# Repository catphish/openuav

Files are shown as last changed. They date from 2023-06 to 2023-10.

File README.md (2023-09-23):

# OpenUAV
OpenUAV is an open source flight controller for multirotors with
a focus on FPV. It is currently in active development.

# Features
* ACRO and ANGLE flight modes
* DSHOT
* ELRS
* Blackbox flight recorder
* USB configuration tool
* Canvas OSD

# Roadmap
* Tidy up and comment all current code
* USB configuration tool
* More OSD options

# Dependencies

## ArchLinux-based distributions

```sh
sudo pacman -Sy arm-none-eabi-binutils arm-none-eabi-gcc arm-none-eabi-newlib \
                dfu-util \
                stlink
```

# Configurator

The USB configurator can be used to configure the quad, and also to download blackbox
logs.

## Configuration

You can view the current configuration by running `configurator get`.

The commands to set configuration are a little cryptic. Use command `configurator set x y z`, where `x` is the
categry number, `y` is the specific entry number, and `z` is the value to set. Please refer to the following file
for the category and entry numbers: https://github.com/catphish/openuav/blob/master/configurator/usb.h

## Motor configuration

The motor configuration is also not very intuitive, but works as follows. First select "props in" `configurator set 3 5 0`
or "props out" `configurator set 3 5 1`.

Next, map the motor outputs using the command: `configurator set 3 x y`, where `x` is the motor output pin (1-4), and `y` is
a corner of the quad according to the following table:

```
0: no output
1: rear left
2: front right
3: front left
4: rear right
```

* NOTE: Due to the way air mode currently works, motors set to zero outout will still spin at minimum RPM. This needs fixing.

## Black Box

Data will be recorded to the black box any time the quad is armed and will continue until the memory
is full (approx 10 minutes flight time). You can erase the black box with `configurator erase`.

You can download the blackbox data with `configurator read > data.csv`. The CSV can be processed
with any tool of your choosing but I find kst2 to be the best.

# Basic Tuning Guide

Tuning should be done in acro mode at a rate you are comfortable with. I use a rate
of 1200 (840 dps) for this process.

## Part 1 - P term

Set the I and D terms to zero so that they don't interfere. Start with a low value (P=50).
Increase P until the quad is sufficiently responsive to stick inputs. You can expect a
little bounceback.
In the 5 inch development quad, the P value is 120.

## Part 2 - D term

Increase the D term only as much as is required to prevent the bounceback.
In the 5 inch development quad, the D value is 150.

## Part 3 - I term

Increase the I term only as much as is required to prevent drift. You may find that this
needs to be increased more when flying in strong wind. Higher values will make the quad
more stable but will introduce some bouncenback when performing flips.
In the 5 inch development quad, the I value is 50.

## Part 4 - Z rates

There is currently no specific process for tuning the Z rates. Values of 200 and 200
for P and I seem to work in most cases. If there is yaw drift then it may be necessary
to increase one or the other. Increase the I term in the case of slow drift or the P
term in the case of sudden yaw disruption.

# Tuning Examples

## TBS Source One V5 5" - 2306/2555KV Motors at 4S

```
Angle rate: 1000
Acro rate: 1000
P: 100
I: 80
D: 100
Yaw P: 200
Yaw I: 100
Expo: 60
Yaw expo: 60
Throttle gain: 80
Throttle min: 200
```

## iFlight iX3 Racer V1 3" - 1104/5250KV Motors at 3S

THIS TUNE IS STILL UNDERGOING TESTING

```
Angle rate (sR): 670
Acro rate (sr): 670
P (sp): x
I (si): x
D (sd): x
Yaw P (sy): 220
Yaw I (sY): 200
Expo (se): 25
Yaw expo (sE): 30
Throttle gain (st): 80
Throttle min (sT): 100
```

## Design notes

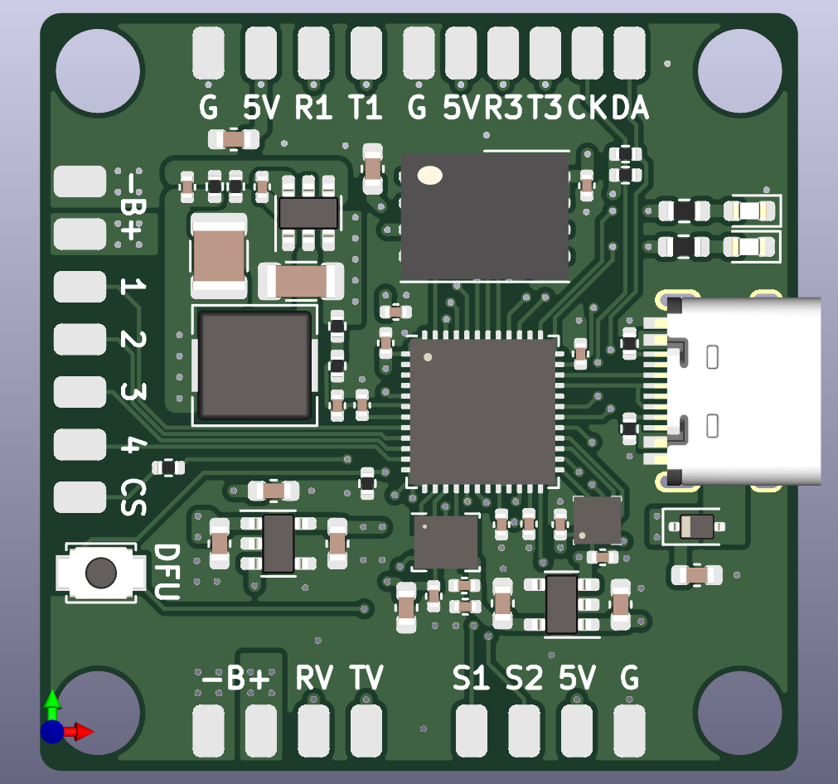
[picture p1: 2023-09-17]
hardware/openuav.png

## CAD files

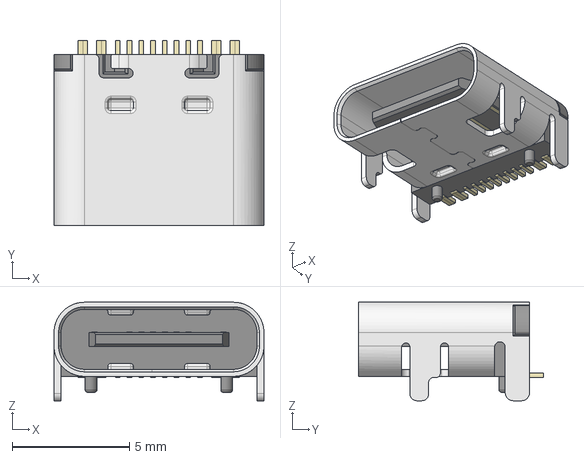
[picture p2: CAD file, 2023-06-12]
hardware/3d/HRO_TYPE-C-31-M-12.step
8.95 x 7.90 x 4.20 mm

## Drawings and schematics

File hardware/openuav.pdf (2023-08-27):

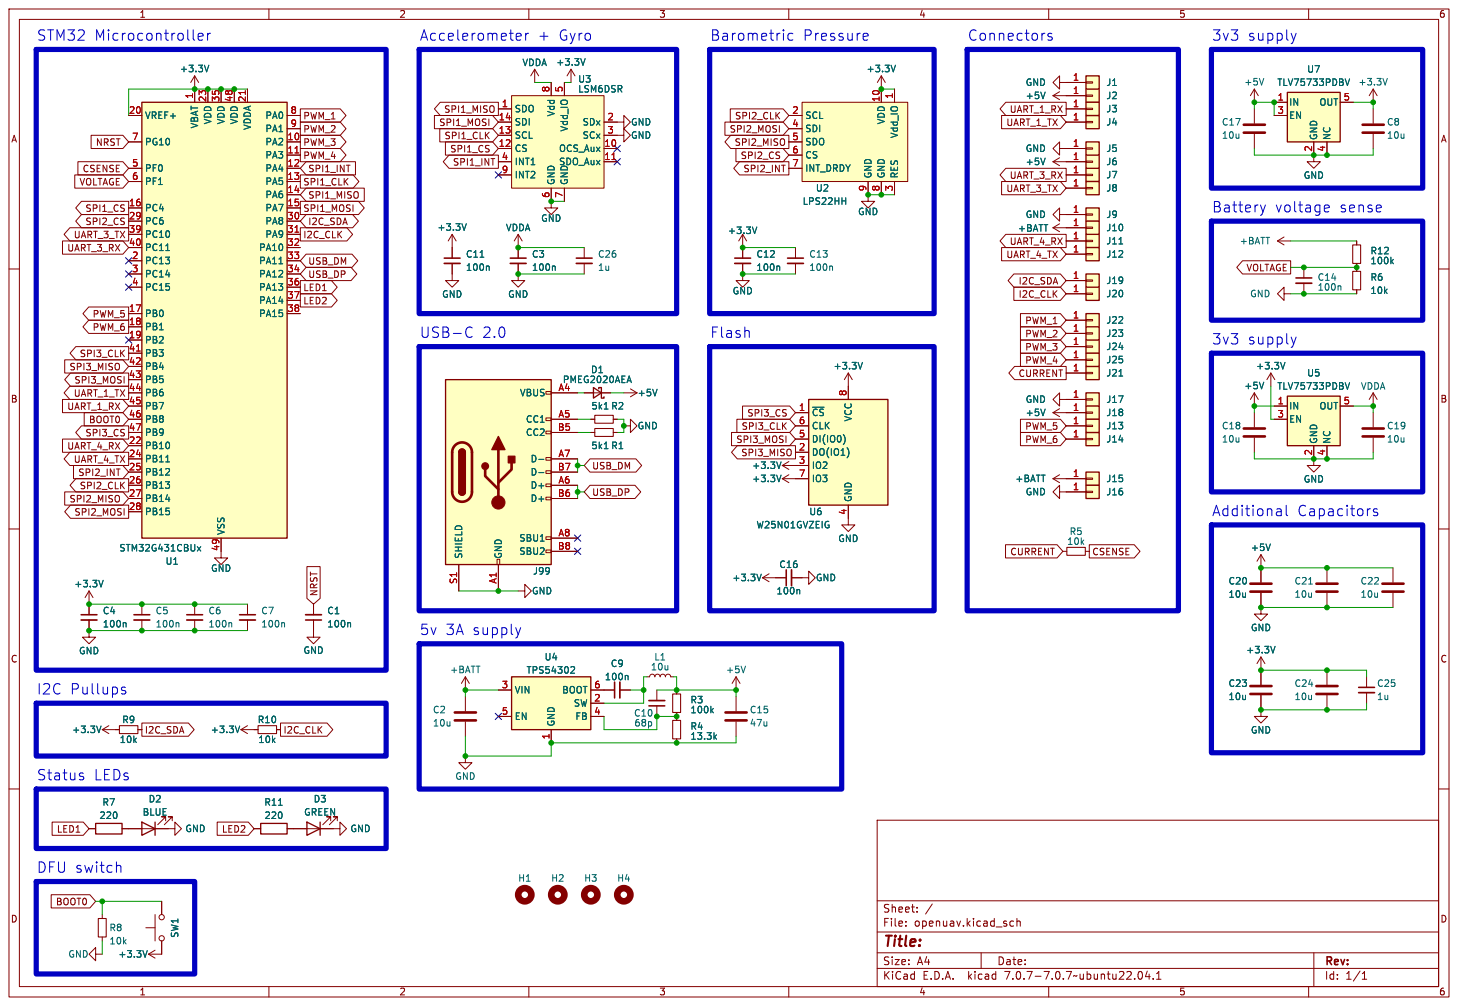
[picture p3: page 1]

1 PA2 10 PA3 11 PA4 12 PA5 13 PA6 14 PA7 15 PC4 16 PB0 17 PB1 18 PB2 19 PC13 2 VREF+ 20 VDDA 21 PB10 22 VDD 23 PB11 24 PB12 25 PB13 26 PB14 27 PB15 28 PC6 29 PC14 3 PA8 30 PA9 31 PA10 32 PA11 33 PA12 34 VDD 35 PA13 36 PA14 37 PA15 38 PC10 39 PC15 4 PC11 40 PB3 41 PB4 42 PB5 43 PB6 44 PB7 45 PB8 46 PB9 47 VDD 48 VSS 49 PF0 5 PF1 6 PG10 7 PA0 8 PA1 9 +3.3V SW1 +3.3V R9

1 PA2 10 PA3 11 PA4 12 PA5 13 PA6 14 PA7 15 PC4 16 PB0 17 PB1 18 PB2 19 PC13 2 VREF+ 20 VDDA 21 PB10 22 VDD 23 PB11 24 PB12 25 PB13 26 PB14 27 PB15 28 PC6 29 PC14 3 PA8 30 PA9 31 PA10 32 PA11 33 PA12 34 VDD 35 PA13 36 PA14 37 PA15 38 PC10 39 PC15 4 PC11 40 PB3 41 PB4 42 PB5 43 PB6 44 PB7 45 PB8 46 PB9 47 VDD 48 VSS 49 PF0 5 PF1 6 PG10 7 PA0 8 PA1 9 U1 STM32G431CBUx R3

1 SW 2 VIN 3 FB 4 EN 5 BOOT 6 U4 +BATT TPS54302

1 SW 2 VIN 3 FB 4 EN 5 BOOT 6 +3.3V R10

Id: 1/1 Title: File: openuav.kicad_sch Sheet: /

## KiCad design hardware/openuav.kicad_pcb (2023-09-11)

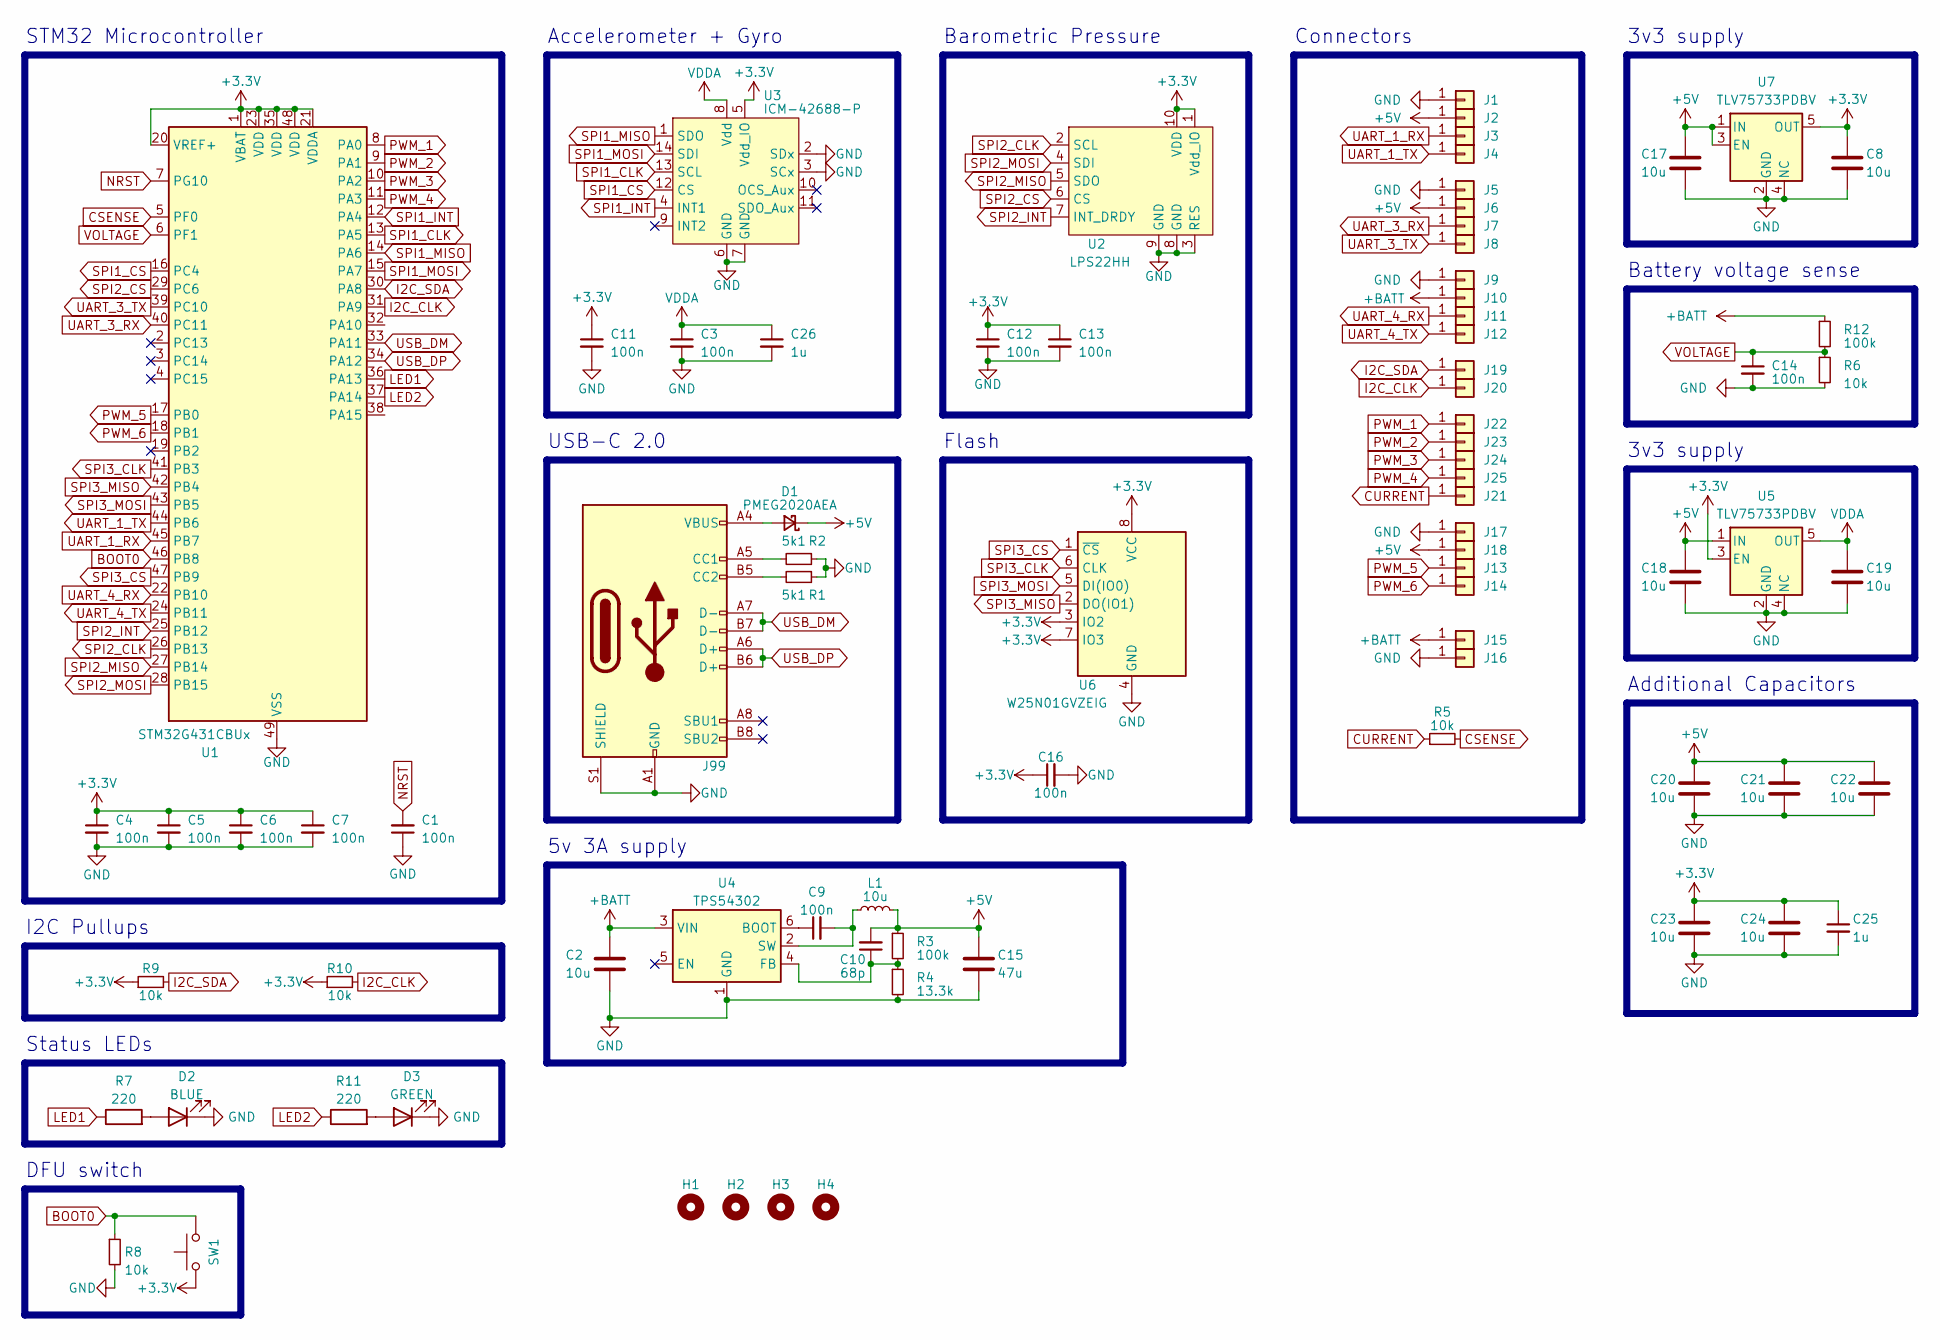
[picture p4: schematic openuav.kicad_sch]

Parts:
C1, C3, C4, C5, C6, C7, C9, C11, C12, C13, C14, C16: 100n; C_0402_1005Metric; LCSC C1525
C2: 10u; C_1206_3216Metric; LCSC C13585
C8, C17, C18, C19, C20, C21, C22, C23, C24: 10u; C_0603_1608Metric; LCSC C19702
C10: 68p; C_0402_1005Metric; LCSC C14441
C15: 47u; C_1210_3225Metric; LCSC C77101
C25, C26: 1u; C_0402_1005Metric; LCSC C52923
D1: PMEG2020AEA; D_SOD-323; LCSC C389354
D2: BLUE; LED_0603_1608Metric; LCSC C72041
D3: GREEN; LED_0603_1608Metric; LCSC C72043
H1, H2, H3, H4: MountingHole; MountingHole_4mm
J1, J2, J3, J4, J5, J6, J7, J8, J9, J10, J11, J12, J13, J14, J15, J16, J17, J18, J19, J20, J21, J22, J23, J24, J25: Conn_01x01; smallpad
J99: USB_C_Receptacle_USB2.0; TYPE-C-31-M-12; LCSC C165948
L1: 10u; L_Sunlord_MWSA0503S; LCSC C408412
R1, R2: 5k1; R_0402_1005Metric; LCSC C25905
R3, R12: 100k; R_0402_1005Metric; LCSC C25741
R4: 13.3k; R_0402_1005Metric; LCSC C274352
R5, R6, R8, R9, R10: 10k; R_0402_1005Metric; LCSC C25744
R7, R11: 220; R_0603_1608Metric; LCSC C22962
SW1: SW_Push; SW_SPST_B3U-1000P; LCSC C231329
U1: STM32G431CBUx; QFN-48-1EP_7x7mm_P0.5mm_EP5.6x5.6mm; LCSC C529356
U2: LPS22HH; ST_HLGA-10_2x2mm_P0.5mm_LayoutBorder3x2y; LCSC C2827824
U3: ICM-42688-P; LGA-14_3x2.5mm_P0.5mm_LayoutBorder3x4y; LCSC C1850418
U4: TPS54302; SOT-23-6; LCSC C311983
U5, U7: TLV75733PDBV; SOT-23-5; LCSC C485517
U6: W25N01GVZEIG; WSON-8-1EP_8x6mm_P1.27mm_EP3.4x4.3mm; LCSC C907680

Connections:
+3V3: C4.1, C5.1, C6.1, C7.1, C8.1, C11.1, C12.1, C13.1, C16.1, C23.1, C24.1, C25.1, R9.1, R10.1, SW1.1, U1.1 (VBAT), U1.20 (VREF+), U1.21 (VDDA), U1.23 (VDD), U1.35 (VDD), U1.48 (VDD), U2.1 (Vdd_IO), U2.10 (VDD), U3.5 (Vdd_IO), U5.3 (EN), U6.3 (IO2), U6.7 (IO3), U6.8 (VCC), U7.5 (OUT)
+5V: C10.2, C15.1, C17.1, C18.1, C20.1, C21.1, C22.1, D1.1 (K), J2.1, J6.1, J18.1, L1.2, R3.1, U5.1 (IN), U7.1 (IN), U7.3 (EN)
+BATT: C2.1, J10.1, J15.1, R12.1, U4.3 (VIN)
BOOT0: R8.1, SW1.2, U1.46 (PB8)
CSENSE: R5.2, U1.5 (PF0)
CURRENT: J21.1, R5.1
GND: C1.1, C2.2, C3.2, C4.2, C5.2, C6.2, C7.2, C8.2, C11.2, C12.2, C13.2, C14.2, C15.2, C16.2, C17.2, C18.2, C19.2, C20.2, C21.2, C22.2, C23.2, C24.2, C25.2, C26.2, D2.1 (K), D3.1 (K), J1.1, J5.1, J9.1, J16.1, J17.1, J99.A1 (GND), J99.A12 (GND), J99.B1 (GND), J99.B12 (GND), J99.S1 (SHIELD), R1.1, R2.1, R4.2, R6.2, R8.2, U1.49 (VSS), U2.3 (RES), U2.8 (GND), U2.9 (GND), U3.2 (SDx), U3.3 (SCx), U3.6 (GND), U3.7 (GND), U4.1 (GND), U5.2 (GND), U5.4 (NC), U6.4 (GND), U7.2 (GND), U7.4 (NC)
I2C_CLK: J20.1, R10.2, U1.31 (PA9)
I2C_SDA: J19.1, R9.2, U1.30 (PA8)
LED1: R7.1, U1.36 (PA13)
LED2: R11.1, U1.37 (PA14)
NRST: C1.2, U1.7 (PG10)
unnamed: D1.2 (A), J99.A4 (VBUS), J99.A9 (VBUS), J99.B4 (VBUS), J99.B9 (VBUS)
unnamed: D2.2 (A), R7.2
unnamed: D3.2 (A), R11.2
unnamed: J99.A5 (CC1), R2.2
unnamed: J99.B5 (CC2), R1.2
unnamed: C9.1, U4.6 (BOOT)
unnamed: C10.1, R3.2, R4.1, U4.4 (FB)
unnamed: C9.2, L1.1, U4.2 (SW)
PWM_1: J22.1, U1.8 (PA0)
PWM_2: J23.1, U1.9 (PA1)
PWM_3: J24.1, U1.10 (PA2)
PWM_4: J25.1, U1.11 (PA3)
PWM_5: J13.1, U1.17 (PB0)
PWM_6: J14.1, U1.18 (PB1)
SPI1_CLK: U1.13 (PA5), U3.13 (SCL)
SPI1_CS: U1.16 (PC4), U3.12 (CS)
SPI1_INT: U1.12 (PA4), U3.4 (INT1)
SPI1_MISO: U1.14 (PA6), U3.1 (SDO)
SPI1_MOSI: U1.15 (PA7), U3.14 (SDI)
SPI2_CLK: U1.26 (PB13), U2.2 (SCL)
SPI2_CS: U1.29 (PC6), U2.6 (CS)
SPI2_INT: U1.25 (PB12), U2.7 (INT_DRDY)
SPI2_MISO: U1.27 (PB14), U2.5 (SDO)
SPI2_MOSI: U1.28 (PB15), U2.4 (SDI)
SPI3_CLK: U1.41 (PB3), U6.6 (CLK)
SPI3_CS: U1.47 (PB9), U6.1 (~CS)
SPI3_MISO: U1.42 (PB4), U6.2 (DO(IO1))
SPI3_MOSI: U1.43 (PB5), U6.5 (DI(IO0))
UART_1_RX: J3.1, U1.45 (PB7)
UART_1_TX: J4.1, U1.44 (PB6)
UART_3_RX: J7.1, U1.40 (PC11)
UART_3_TX: J8.1, U1.39 (PC10)
UART_4_RX: J11.1, U1.22 (PB10)
UART_4_TX: J12.1, U1.24 (PB11)
USB_DM: J99.A7 (D-), J99.B7 (D-), U1.33 (PA11)
USB_DP: J99.A6 (D+), J99.B6 (D+), U1.34 (PA12)
VDDA: C3.1, C19.1, C26.1, U3.8 (Vdd), U5.5 (OUT)
VOLTAGE: C14.1, R6.1, R12.2, U1.6 (PF1)

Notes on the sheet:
Accelerometer + Gyro
DFU switch
Status LEDs
3v3 supply
Additional Capacitors
5v 3A supply
Flash
Barometric Pressure
STM32 Microcontroller
Connectors
I2C Pullups
USB-C 2.0
Battery voltage sense

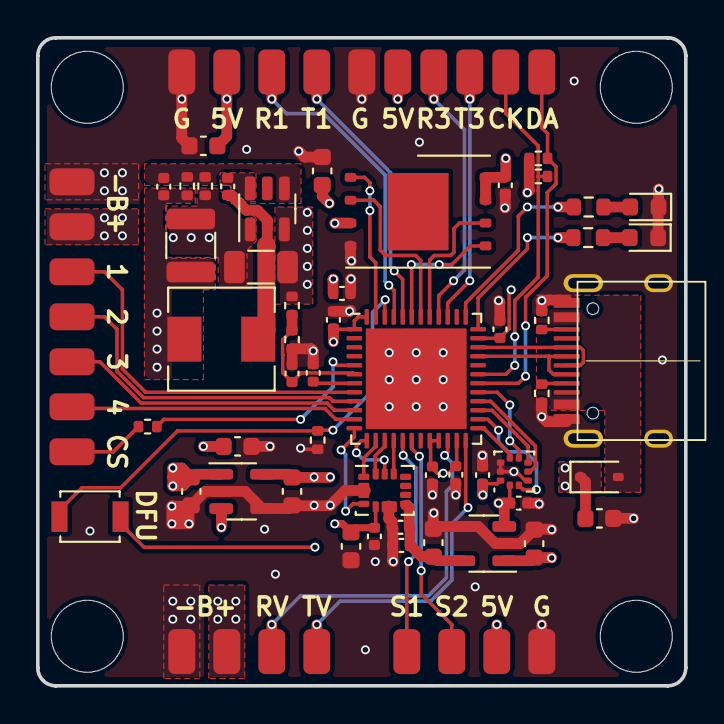
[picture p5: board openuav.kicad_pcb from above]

Board: 4 copper layers, 36.0 x 36.0 mm, 80 parts (0 on the bottom side), 50 nets.

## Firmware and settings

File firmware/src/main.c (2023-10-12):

#include <stm32g4xx.h>
#include <string.h>
#include <stdio.h>
#include <stdint.h>
#include "gpio.h"
#include "usb.h"
#include "dshot.h"
#include "led.h"
#include "util.h"
#include "spi.h"
#include "elrs.h"
#include "uart.h"
#include "clock.h"
#include "gyro.h"
#include "imu.h"
#include "quaternion.h"
#include "adc.h"
#include "msp.h"
#include "settings.h"
#include "flash.h"
#include "blackbox.h"
#include "airmode.h"
#include "main.h"
#include "barometer.h"

// Set up all the hardware. Each part of the hardware has its own
// module of code with its own init function.
void SystemInit(void) {
  clock_init();
  msleep(200);
  gpio_init();
  led_init();
  usb_init();
  dshot_init();
  spi_init();
  uart_init();
  gyro_init();
  imu_zero();
  baro_init();
  adc_init();
  flash_init();
  blackbox_init();
}

// This struct contains the data that will be output to the four motors.
static struct dshot_data dshot;

// Create a ring buffer of the last GYRO_BUFFER_SIZE gyro readings.
// This will be used to calculate the D term.
#define GYRO_BUFFER_SIZE 60
static struct gyro_data gyro_buffer[GYRO_BUFFER_SIZE];
static uint8_t gyro_buffer_index = 0;

int main(void) {
  // This flag inhibits arming at power-on, and is set to 1 when it's safe to arm.
  uint8_t arming_allowed = 0;

  // These variables are used to store the accumulated integral term for each axis.
  float i_pitch = 0;
  float i_roll  = 0;
  float i_yaw   = 0;

  // A counter to keep track of the number of frames since arming. Used only by the gyro calibration routine.
  uint32_t arm_counter = 0;

  // A continuously increasing counter that is used to timestamp blackbox frames.
  uint32_t frame_count = 0;

  // LED2 is the power LED, turn it on before we do anything else.
  led2_on();

  // Load settings from flash.
  settings_read();

  // Main loop. This runs as fast as possible, but the majority of the code is located
  // within an if block that only runs each time data is received from the gyro.
  while(1) {
    // Poll the USB peripheral to transmit and receive data as needed.
    usb_main();
    // Poll the UART peripheral to transmit pending data. Receiving of data is handled by interrupts.
    uart_tx();
    // Process MSP requests and transmit responses. This also transmits OSD data.
    msp_send_response();

    // Each time the gyro has new data, we run the main control loop.
    if(gyro_ready()) {
      // Fetch settings and scale them to the appropriate units.
      volatile struct settings *settings = settings_get();
      float angle_rate    = 10.f      * settings->angle_rate;
      float acro_rate     = 0.01f     * settings->acro_rate;
      float p             = 0.001f    * settings->p;
      float i             = 0.000001f * settings->i;
      float d             = 0.001f    * settings->d;
      float yaw_p         = 0.001f    * settings->yaw_p;
      float yaw_i         = 0.000001f * settings->yaw_i;
      float expo          = 0.01f     * settings->expo;
      float yaw_expo      = 0.01f     * settings->yaw_expo;
      float throttle_gain = 0.01f     * settings->throttle_gain;
      float throttle_min  =             settings->throttle_min;

      // If we have valid ELRS data and it indicates that we're currently disarmed, then we
      // set a flag to allow arming. This prevents accidental arming at power-on.
      if(elrs_valid() && elrs_channel(4) < 0) {
        arming_allowed = 1;
      }

      // If we have valid ELRS data, and the arming switch is set,
      // and we've prevously disarmed, go ahead and start the motors.
      if(elrs_valid() && elrs_channel(4) > 0 && arming_allowed) {
        // LED1 indicates the arming state.
        led1_on();
        // If we've been armed for less than 200 cycles, don't actually arm the
        // motors yet. Instead, spend a a short time calibrating the gyro.
        if(arm_counter < 200) {
          gyro_calibrate();
          arm_counter++;
          dshot.armed = 0;
        } else {
          // Gyro calibration is finished.
          // Set the armed flag in the DSHOT output to 1.
          dshot.armed = 1;
        }
      } else {
        // LED1 indicates the arming state.
        led1_off();
        // Set the armed flag in the DSHOT output to 0.
        dshot.armed = 0;
        // If we are not armed, reset the integral terms.
        i_pitch = 0;
        i_roll  = 0;
        i_yaw   = 0;
        // Reset the arm counter and gyro calibration.
        arm_counter = 0;
        gyro_zero();
        // Zero the IMU orientation.
        // We assume that when we're disarmed, we're sitting on a level surface.
        imu_zero();
      }

      // Call elrs_tick() at regular intervals. This allows it to count down an internal
      // timer to implement failsafe behavior if no ELRS data is received.
      elrs_tick();

      // These structs will contain the gyro and accelerometer data.
      struct gyro_data gyro;
      struct gyro_data accel;

      // Read the gyro and accelerometer data.
      gyro_read(&gyro);
      accel_read(&accel);

      // The IMU uses input from both the gyro and accelerometer to estimate the orientation.
      // Update the IMU using the gyro and accelerometer data.
      imu_update_from_gyro(&gyro);
      imu_update_from_accel(&accel);

      // These variables will store the requested rotation rate for each axis.
      // The units of these variables are gyro units. 16.4 units = 1 degree per second.
      int32_t rotation_request_pitch = 0;
      int32_t rotation_request_roll  = 0;
      int32_t rotation_request_yaw   = 0;

      // Set the throttle. We take the throttle channel from the transmitter, offset it
      // by 820 so that it's zero at the bottom rather than the midpoint. Then we scale
      // it by the throttle gain and add the minimum throttle.
      int32_t throttle = throttle_gain * (elrs_channel(2) + 820) + throttle_min;

      // AUX2 is the mode switch. If it's high, we're in angle mode, otherwise we're in rate mode.
      if(elrs_channel(5) > 0) {
        // Angle mode

        // Get the current X and Y tilt angles from the IMU in radians.
        float tilt_pitch, tilt_roll;
        imu_get_xy_tilt(&tilt_pitch, &tilt_roll);

        // Normalize and limit the elrs input to +/- 1.
        float target_pitch = elrs_channel(1) / 820.f;
        float target_roll  = elrs_channel(0) / 820.f;
        if(target_pitch >  1.f) target_pitch =  1.f;
        if(target_pitch < -1.f) target_pitch = -1.f;
        if(target_roll  >  1.f) target_roll  =  1.f;
        if(target_roll  < -1.f) target_roll  = -1.f;

        // Map the input values from a square to a circle.
        target_pitch = target_pitch * sqrtf(1.f - target_roll * target_roll / 2.f);
        target_roll  = target_roll  * sqrtf(1.f - target_pitch * target_pitch / 2.f);

        // Multiply the input angles by the configured angle limit to get the target angles.
        // Currently the limit is hardcoded to 1 radian.
        target_pitch *= 1.f;
        target_roll  *= 1.f;

        // Subtract the tilt angle from the requested angle to get the angle error.
        float angle_error_pitch = target_pitch - tilt_pitch;
        float angle_error_roll  = target_roll  - tilt_roll;

        // Multiply the angle error by the configured angle rate to get the required rotation rate.
        rotation_request_pitch = angle_error_pitch * angle_rate;
        rotation_request_roll  = angle_error_roll  * angle_rate;
        rotation_request_yaw   = elrs_channel(3)   * acro_rate;
      } else {
        // Rate mode.
        // Apply expo to roll input.
        // TODO: split expo into a separate function.
        float transmitter_roll = elrs_channel(0);
        if(transmitter_roll >  820) transmitter_roll =  820;
        if(transmitter_roll < -820) transmitter_roll = -820;
        transmitter_roll = expo * transmitter_roll * transmitter_roll * transmitter_roll / 820.f / 820.f + (1.f - expo) * transmitter_roll;
        // Apply expo to pitch input.
        float transmitter_pitch = elrs_channel(1);
        if(transmitter_pitch >  820) transmitter_pitch =  820;
        if(transmitter_pitch < -820) transmitter_pitch = -820;
        transmitter_pitch = expo * transmitter_pitch * transmitter_pitch * transmitter_pitch / 820.f / 820.f + (1.f - expo) * transmitter_pitch;
        // Apply expo to yaw input.
        float transmitter_yaw = elrs_channel(3);
        if(transmitter_yaw >  820) transmitter_yaw =  820;
        if(transmitter_yaw < -820) transmitter_yaw = -820;
        transmitter_yaw = yaw_expo * transmitter_yaw * transmitter_yaw * transmitter_yaw / 820.f / 820.f + (1.f - yaw_expo) * transmitter_yaw;

        // Multiply the transmitter input by the configured acro rate to get the final rotation rate.
        rotation_request_pitch = transmitter_pitch * acro_rate;
        rotation_request_roll  = transmitter_roll  * acro_rate;
        rotation_request_yaw   = transmitter_yaw   * acro_rate;
      }

      // Calculate the error in angular velocity by subtracting the gyro readings from the requested
      // angular velocity. It looks like an additon but the gyro values are negative.
      int32_t error_pitch = p     * (gyro.x + rotation_request_pitch);
      int32_t error_roll  = p     * (gyro.y + rotation_request_roll);
      int32_t error_yaw   = yaw_p * (gyro.z + rotation_request_yaw);

      // Put the current gyro value into the ring buffer. This allows us to compare
      // it with previous gyro values to calculate the D term below.
      gyro_buffer[gyro_buffer_index] = gyro;
      // Increment the ring buffer index, and wrap it around if necessary.
      gyro_buffer_index++; if(gyro_buffer_index >= GYRO_BUFFER_SIZE) gyro_buffer_index = 0;

      // Calculate the difference between the current gyro value and the value from GYRO_BUFFER_SIZE loops
      // ago to find the rate of change in the gyro data, and multiply by the D gain to get the D term.
      float d_pitch = (gyro.x - gyro_buffer[gyro_buffer_index].x) * d;
      float d_roll  = (gyro.y - gyro_buffer[gyro_buffer_index].y) * d;

      // Integrate the error in each axis.
      // Don't integrate pitch and roll if the D term exceeds a specified limit.
      if(d_pitch < 100 && d_pitch > -100)
        i_pitch += i * (gyro.x + rotation_request_pitch);

      if(d_roll < 100 && d_roll > -100)
        i_roll  += i     * (gyro.y + rotation_request_roll);

      i_yaw   += yaw_i * (gyro.z + rotation_request_yaw);

      // Calculate the motor outputs. The motor_outputs array contains the following elements.
      // 0: no output
      // 1: rear left
      // 2: front right
      // 3: front left
      // 4: rear right
      int32_t motor_outputs[5];
      // Motor zero is always off. This provides a convenient way to disable motors during configuration and testing.
      motor_outputs[0] = 0;
      // The yaw calculations need to be different for a props-in configuration vs a props-out configuration.
      if(settings->motor_direction) {
        // Props out
        motor_outputs[1] = throttle + error_pitch + error_roll - error_yaw + i_pitch + i_roll - i_yaw + d_pitch + d_roll;
        motor_outputs[2] = throttle - error_pitch - error_roll - error_yaw - i_pitch - i_roll - i_yaw - d_pitch - d_roll;
        motor_outputs[3] = throttle - error_pitch + error_roll + error_yaw - i_pitch + i_roll + i_yaw - d_pitch + d_roll;
        motor_outputs[4] = throttle + error_pitch - error_roll + error_yaw + i_pitch - i_roll + i_yaw + d_pitch - d_roll;
      } else {
        // Props in
        motor_outputs[1] = throttle + error_pitch + error_roll + error_yaw + i_pitch + i_roll + i_yaw + d_pitch + d_roll;
        motor_outputs[2] = throttle - error_pitch - error_roll + error_yaw - i_pitch - i_roll + i_yaw - d_pitch - d_roll;
        motor_outputs[3] = throttle - error_pitch + error_roll - error_yaw - i_pitch + i_roll - i_yaw - d_pitch + d_roll;
        motor_outputs[4] = throttle + error_pitch - error_roll - error_yaw + i_pitch - i_roll - i_yaw + d_pitch - d_roll;
      }

      // Activate air mode to keep motor outputs within a good range while maintaining differential.
      air_mode(motor_outputs);

      // Map the appropriate motor output to each DSHOT channel.
      dshot.motor1 = motor_outputs[settings->motor1];
      dshot.motor2 = motor_outputs[settings->motor2];
      dshot.motor3 = motor_outputs[settings->motor3];
      dshot.motor4 = motor_outputs[settings->motor4];

      // Write the motor outputs to the ESCs.
      dshot_write(&dshot);

      // Prepare a blackbox data frame to log the data for this loop iteration.
      struct blackbox_frame blackbox_data;
      blackbox_data.timestamp = frame_count;
      blackbox_data.setpoint[0] = rotation_request_pitch;
      blackbox_data.setpoint[1] = rotation_request_roll;
      blackbox_data.setpoint[2] = rotation_request_yaw;
      blackbox_data.gyro_data[0] = gyro.x;
      blackbox_data.gyro_data[1] = gyro.y;
      blackbox_data.gyro_data[2] = gyro.z;
      blackbox_data.p[0] = error_pitch;
      blackbox_data.p[1] = error_roll;
      blackbox_data.p[2] = error_yaw;
      blackbox_data.i[0] = i_pitch;
      blackbox_data.i[1] = i_roll;
      blackbox_data.i[2] = i_yaw;
      blackbox_data.d[0] = d_pitch;
      blackbox_data.d[1] = d_roll;
      blackbox_data.d[2] = 0;
      blackbox_data.motor[0] = dshot.motor1;
      blackbox_data.motor[1] = dshot.motor2;
      blackbox_data.motor[2] = dshot.motor3;
      blackbox_data.motor[3] = dshot.motor4;

      // If we're armed, write the log data to the blackbox.
      if(dshot.armed) blackbox_write(&blackbox_data);

      // Increment the loop counter
      frame_count++;
    }
  }
  // This should never be reached.
  return 0;
}

// Return whether the quad is currently armed.
int main_get_armed_state() {
  return dshot.armed;
}

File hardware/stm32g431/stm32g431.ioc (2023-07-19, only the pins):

Mcu.UserName=STM32G431CBUx
PA0.Signal=S_TIM2_CH1
PA1.Signal=S_TIM2_CH2
PA10.GPIO_Label=LED2
PA10.Signal=GPIO_Output
PA11.Signal=USB_DM
PA12.Signal=USB_DP
PA13.Signal=SYS_JTMS-SWDIO
PA14.Signal=SYS_JTCK-SWCLK
PA15.GPIO_Label=SPI3_CS
PA15.Signal=GPIO_Output
PA2.Signal=S_TIM2_CH3
PA3.Signal=S_TIM2_CH4
PA4.GPIO_Label=SPI1_INT
PA4.Signal=GPXTI4
PA5.Signal=SPI1_SCK
PA6.Signal=SPI1_MISO
PA7.Signal=SPI1_MOSI
PA8.Signal=I2C2_SDA
PA9.Signal=I2C2_SCL
PB0.Signal=S_TIM3_CH3
PB1.Signal=S_TIM3_CH4
PB10.Signal=LPUART1_RX
PB11.Signal=LPUART1_TX
PB12.GPIO_Label=SPI2_INT
PB12.Signal=GPXTI12
PB13.Signal=SPI2_SCK
PB14.Signal=SPI2_MISO
PB15.Signal=SPI2_MOSI
PB3.Signal=SPI3_SCK
PB4.Signal=SPI3_MISO
PB5.Signal=SPI3_MOSI
PB6.Signal=USART1_TX
PB7.Signal=USART1_RX
PB9.GPIO_Label=LED1
PB9.Signal=GPIO_Output
PC10.Signal=USART3_TX
PC11.Signal=USART3_RX
PC4.GPIO_Label=SPI1_CS
PC4.Signal=GPIO_Output
PC6.GPIO_Label=SPI2_CS
PC6.Signal=GPIO_Output
PF0-OSC_IN.Signal=ADC1_IN10
PF1-OSC_OUT.Signal=ADC2_IN10

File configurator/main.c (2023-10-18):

#include <stdio.h>
#include <stdlib.h>
#include <string.h>
#include <unistd.h>
#include <stdint.h>
#include <libusb.h>

#include "usb.h"

void get_all(void) {
  int value, raw_value;

  printf("          1. TUNING\n");
  value = get_setting(USB_SETTING_CAT_TUNE, USB_SETTING_TUNE_P);
  printf("            P: %d\n", value);
  value = get_setting(USB_SETTING_CAT_TUNE, USB_SETTING_TUNE_I);
  printf("            I: %d\n", value);
  value = get_setting(USB_SETTING_CAT_TUNE, USB_SETTING_TUNE_D);
  printf("            D: %d\n", value);
  value = get_setting(USB_SETTING_CAT_TUNE, USB_SETTING_TUNE_YAW_P);
  printf("        Yaw P: %d\n", value);
  value = get_setting(USB_SETTING_CAT_TUNE, USB_SETTING_TUNE_YAW_I);
  printf("        Yaw I: %d\n", value);

  printf("\n          2. CONTROL\n");
  value = get_setting(USB_SETTING_CAT_CONTROL, USB_SETTING_CONTROL_ANGLE_RATE);
  printf("    Angle Rate: %d\n", value);
  value = get_setting(USB_SETTING_CAT_CONTROL, USB_SETTING_CONTROL_ACRO_RATE);
  printf("     Acro Rate: %d\n", value);
  value = get_setting(USB_SETTING_CAT_CONTROL, USB_SETTING_CONTROL_EXPO);
  printf("          Expo: %d\n", value);
  value = get_setting(USB_SETTING_CAT_CONTROL, USB_SETTING_CONTROL_YAW_EXPO);
  printf("      Yaw Expo: %d\n", value);
  value = get_setting(USB_SETTING_CAT_CONTROL, USB_SETTING_CONTROL_THROTTLE_GAIN);
  printf(" Throttle Gain: %d\n", value);
  value = get_setting(USB_SETTING_CAT_CONTROL, USB_SETTING_CONTROL_THROTTLE_MIN);
  printf("  Throttle Min: %d\n", value);
  printf("(1 rate unit = 0.6097561 DPS, so DPS*(1/0.6097561) will give desired value)\n");

  printf("\n          3. MOTOR\n");
  value = get_setting(USB_SETTING_CAT_MOTOR, USB_SETTING_MOTOR_1);
  printf("       Motor1: %d\n", value);
  value = get_setting(USB_SETTING_CAT_MOTOR, USB_SETTING_MOTOR_2);
  printf("       Motor2: %d\n", value);
  value = get_setting(USB_SETTING_CAT_MOTOR, USB_SETTING_MOTOR_3);
  printf("       Motor3: %d\n", value);
  value = get_setting(USB_SETTING_CAT_MOTOR, USB_SETTING_MOTOR_4);
  printf("       Motor4: %d\n", value);
  value = get_setting(USB_SETTING_CAT_MOTOR, USB_SETTING_MOTOR_DIRECTION);
  printf("    Direction: %d\n", value);
  printf("(1: rear left, 2: front right, 3: front left, 4: rear right)\n");

  printf("\n          4. BATTERY\n");
  value = get_setting(USB_SETTING_CAT_BATT, USB_SETTING_BATT_CELL_COUNT);
  printf("   Cell Count: %d\n", value);
  value = get_setting(USB_SETTING_CAT_BATT, USB_SETTING_BATT_ADC1_COEFFICIENT);
  raw_value = get_setting(USB_SETTING_CAT_BATT, USB_VALUE_ADC1_RAW);
  printf("   ADC1 coeff: %d (current raw value: %d)\n", value, raw_value);
  value = get_setting(USB_SETTING_CAT_BATT, USB_SETTING_BATT_ADC2_COEFFICIENT);
  raw_value = get_setting(USB_SETTING_CAT_BATT, USB_VALUE_ADC2_RAW);
  printf("   ADC2 coeff: %d (current raw value: %d)\n", value, raw_value);
  printf("(raw value * coefficient / 1000 will give the mV/mA figure)\n");
}

int main(int argc, char *argv[])
{
  if (usb_init()) return 1;

  if (argc == 1) {
    printf("Usage: %s <command> [args]\n", argv[0]);
    printf("Commands:\n");
    printf("  get <category> <index>\n");
    printf("  set <category> <index> <value>\n");
    printf("  save\n");
    printf("  load\n");
    printf("  read <address>\n");
    printf("  erase\n");
    return 0;
  }

  if(strcmp(argv[1], "get") == 0) {
    if(argc == 4) {
      uint8_t category = atoi(argv[2]);
      uint8_t index = atoi(argv[3]);
      uint32_t value = get_setting(category, index);
      printf("%d\n", value);
    } else {
      get_all();
    }
  } else if(strcmp(argv[1], "set") == 0) {
    if(argc != 5) {
      printf("Usage: %s set <category> <index> <value>\n", argv[0]);
      return 1;
    }
    uint8_t category = atoi(argv[2]);
    uint8_t index = atoi(argv[3]);
    uint32_t value = atoi(argv[4]);
    set_setting(category, index, value);
  } else if(strcmp(argv[1], "save") == 0) {
    if(argc != 2) {
      printf("Usage: %s save\n", argv[0]);
      return 1;
    }
    save_settings();
  } else if(strcmp(argv[1], "load") == 0) {
    if(argc != 2) {
      printf("Usage: %s load\n", argv[0]);
      return 1;
    }
    load_settings();
  } else if(strcmp(argv[1], "read") == 0) {
    uint32_t prev_time = 0;
    printf("time,gyro[0],gyro[1],gyro[2],target[0],target[1],target[2],m[0],m[1],m[2],m[3],p[0],p[1],p[2],i[0],i[1],i[2],d[0],d[1],d[2]\n");
    for(int address=0; address<1024*1024*128; address+=64) {
      uint8_t data[64];
      read_flash(address, data);
      read_flash(address+32, data+32);
      uint32_t time = data[0] | (data[1] << 8) | (data[2] << 16) | (data[3] << 24);
      if(time == 0xFFFFFFFF) break;
      if(time > prev_time) {
        float timef = time;
        timef /= 8000.f;
        printf("%f", timef);
        for(int n=0; n<19;n++) {
          int16_t v = data[2*n+4] | (data[2*n+5] << 8);
          int32_t value = v;
          if(n<3) value *= -1;
          if(n>=7 && n<=10) value *= 10;
          if(n>9) value *= 10;
          printf(",%i", value);
        }
        printf("\n");
        prev_time = time;
      }
    }
  } else if(strcmp(argv[1], "erase") == 0) {
    printf("Erasing flash ");
    for(int block=0; block<1024; block++) {
      printf(".");
      fflush(stdout);
      erase_flash(block);
    }
    printf(" Done\n");
  } else {
    printf("Unknown command: %s\n", argv[1]);
    return 1;
  }

  usb_close();
}

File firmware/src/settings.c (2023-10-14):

#include <stm32g4xx.h>
#include "settings.h"
#include "usb.h"
#include "adc.h"

#define VERSION 2

volatile struct settings settings;

void settings_default() {
  settings.version          = VERSION;
  settings.angle_rate       = 800;   // 8.0
  settings.acro_rate        = 800;   // 8.0
  settings.p                = 100;   // 0.1
  settings.i                = 200;   // 0.0002
  settings.d                = 100;   // 0.1
  settings.yaw_p            = 100;   // 0.1
  settings.yaw_i            = 200;   // 0.0001
  settings.expo             = 50;    // 0.5
  settings.yaw_expo         = 50;    // 0.5
  settings.throttle_gain    = 80;    // 0.8
  settings.throttle_min     = 200;   // 200
  settings.motor_direction  = 0;     // Props IN
  settings.motor1           = 0;     // Default disabled
  settings.motor2           = 0;     // Default disabled
  settings.motor3           = 0;     // Default disabled
  settings.motor4           = 0;     // Default disabled
  settings.adc1_coefficient = 2150;  // 2150 as calibrated by sixtyfive on v4 board
  settings.adc2_coefficient = 565;   // 565 as calibrated by catphish on v3 board
  settings.cell_count       = 0;
  settings.checksum         = 0;
}

void settings_read() {
  // Load the settings from flash at (FLASH_BASE + 31 * 0x800) into the settings struct.
  // If the settings are invalid, set them to default values.
  struct settings *flash = (struct settings *)(FLASH_BASE + 31 * 0x800);
  // Calculate the checksum of the settings struct.
  uint32_t checksum = 0;
  for(uint32_t i = 0; i < sizeof(struct settings) - 4; i++) {
    checksum += ((uint8_t *)flash)[i];
  }
  // If the checksum is valid, apply the settings, else set the defaults.
  if(flash->version == VERSION && checksum == flash->checksum) {
    settings = *flash;
  } else {
    settings_default();
  }
}

void settings_save() {
  settings.checksum = 0;
  for(uint32_t i = 0; i < sizeof(struct settings) - sizeof(uint32_t); i++) {
    settings.checksum += ((uint8_t *)&settings)[i];
  }

  __disable_irq();
  // Wait for flash to be ready
  while(FLASH->SR & FLASH_SR_BSY);
  // Unlock flash memory
  if(FLASH->CR & FLASH_CR_LOCK) {
    FLASH->KEYR = 0x45670123U;
    FLASH->KEYR = 0xCDEF89ABU;
  }
  // Wait for flash to be ready
  while(FLASH->SR & FLASH_SR_BSY);
  // Erase page 31
  FLASH->CR |= FLASH_CR_PER;
  FLASH->CR |= (31 << FLASH_CR_PNB_Pos);
  FLASH->CR |= FLASH_CR_STRT;
  // Wait for flash to be ready
  while(FLASH->SR & FLASH_SR_BSY);
  // Write settings to flash
  FLASH->CR &= ~FLASH_CR_PER;
  FLASH->CR |= FLASH_CR_PG;
  for(uint32_t i = 0; i < sizeof(struct settings) / sizeof(uint32_t); i++) {
    *(volatile uint32_t *)(FLASH_BASE + 31 * 0x800 + i * sizeof(uint32_t)) = ((uint32_t *)&settings)[i];
    // Wait for flash to be ready
    while(FLASH->SR & FLASH_SR_BSY);
  }
  // Lock flash memory
  FLASH->CR = FLASH_CR_LOCK;
  __enable_irq();
}

volatile struct settings *settings_get() {
  return &settings;
}

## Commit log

2023-04-19 Initial commit, dev board
    [openuav.kicad_pcb, openuav.kicad_sch]
2023-04-21 Work in progress on more complete schematic
    [openuav.kicad_pcb, openuav.kicad_sch]
2023-04-21 Continued work in progress on initial design
    [openuav.kicad_pcb, openuav.kicad_sch]
2023-04-21 Change OSD to 3v3, align pads to edge
    [openuav.kicad_pcb, openuav.kicad_sch]
2023-04-23 start to rethink power supplies
    [openuav.kicad_pcb, openuav.kicad_sch]
2023-04-23 remove power supply, start over
    [openuav.kicad_pcb, openuav.kicad_sch]
2023-04-24 Add new 5V SMPS. Rearrange MCU pins to support 3 x SPI
    [openuav.kicad_pcb, openuav.kicad_sch]
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2023-04-30 Finish blending ELRS and gyro into motors, split code out into files
2023-04-30 work on layout with JST-SH connectors
    [SM04B-SRSS-TB.STEP, SM06B-SRSS-TB.STEP, SM08B-SRSS-TB.STEP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]
2023-05-01 finish basic board layout
    [openuav.kicad_pcb, openuav.kicad_sch]
2023-05-03 new PCB WIP
    [openuav.kicad_pcb, openuav.kicad_sch]
2023-05-04 Finish draft PCB design
    [openuav.kicad_pcb, openuav.kicad_sch]
2023-05-04 improved sinkscreen and readme
    [openuav.kicad_pcb]
2023-05-04 Add buzzer connection, minor layout improvements
    [openuav.kicad_pcb, openuav.kicad_sch]
2023-05-04 update schematic with buzzer
2023-05-04 increase density
    [openuav.kicad_pcb]
2023-05-04 fix 3v3/3.3v confusion, make gyro pinout compatble with BMI270
    [openuav.kicad_pcb, openuav.kicad_sch]
2023-05-05 Improve connector spacing and thermal management
    [openuav.kicad_pcb, openuav.kicad_sch]
2023-05-05 tiny layout fix
    [openuav.kicad_pcb]
2023-05-05 update ioc file with all pins, add pulldown on boot0
    [openuav.kicad_pcb, openuav.kicad_sch]
2023-05-05 final touches to pcb
    [openuav.kicad_pcb]
2023-05-05 add note about TT pin
    [openuav.kicad_pcb, openuav.kicad_sch]
2023-05-05 Replace ST parts with BMI270 and BMP280
    [openuav.kicad_pcb, openuav.kicad_sch]
2023-05-05 Label pins in cubemx, remove redundant BARO interrupt pin label
    [openuav.kicad_sch]
2023-05-05 Add missing JLC part numbers
    [openuav.kicad_pcb, openuav.kicad_sch]
2023-05-05 Increase all vias to 0.3/0.5
    [openuav.kicad_pcb]
2023-05-06 Remove unused connector 3D models
    [SM04B-SRSS-TB.STEP, SM06B-SRSS-TB.STEP, SM08B-SRSS-TB.STEP]
2023-05-06 fix JLC 10k resistor part numbers
    [openuav.kicad_sch]
2023-05-17 begin work on STM32G474 version
    [openuav.kicad_sch]
2023-05-17 continue g474 redesign
    [openuav.kicad_pcb, openuav.kicad_sch]
2023-05-17 continued work on G474 board
    [openuav.kicad_pcb, openuav.kicad_sch]
2023-05-18 continues work on G474 layout TODO: the pin space is 2.5mm not 2.54mm
    [TS-1187A-B-A-B.step, openuav.kicad_pcb, openuav.kicad_sch]
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2023-05-22 finish G474 layout, add buzzer buffer, add pullups, fix pin spacing
    [openuav.kicad_pcb, openuav.kicad_sch]
2023-05-22 add heatsink copper to inductor
    [openuav.kicad_pcb]
2023-05-22 rearrange buzzer pins to keep +5v away from USB GND
    [openuav.kicad_pcb]
2023-05-23 add vtx power switch, use smaller dfu button
    [openuav.kicad_pcb, openuav.kicad_sch]
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2023-06-11 start work again on g431 board
    [openuav.kicad_pcb, openuav.kicad_sch]
2023-06-11 Remove old files
    [TS-1187A-B-A-B.step]
2023-06-11 major work on G431
    [openuav.kicad_pcb, openuav.kicad_sch]
2023-06-12 WIP on G431 layout
    [openuav.kicad_pcb, openuav.kicad_sch]
2023-06-12 more on g431 board
    [HRO_TYPE-C-31-M-12.step, openuav.kicad_pcb, openuav.kicad_sch]
2023-06-13 finish g431 design
    [openuav.kicad_pcb, openuav.kicad_sch]
2023-06-13 add tiny i2c magnetometer board
    [magnetometer.kicad_pcb, magnetometer.kicad_sch]
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2023-07-19 Fix pin configuration for pin 8
    [gpio.c]
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2023-07-21 Fix power supply capacitor in schematic
    [openuav.kicad_sch]
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2023-07-31 Fix LED polarity, move OSD out of interrupt and add voltage, more tuning
    [adc.c, led.c, main.c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]
2023-08-01 remove unused code, fix timing
    [main.c]
2023-08-01 Fix layout for SMPS feedback capacitor
    [openuav.kicad_pcb]
2023-08-01 remove copper under inductor
    [openuav.kicad_pcb]
2023-08-02 Make motor mappings and prop configuration much clearer. Improve voltage string handling.
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2023-08-02 Remove magnetometer PCB, never really started
    [magnetometer.kicad_pcb, magnetometer.kicad_sch]
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2023-08-06 Remove debug port
    [openuav.kicad_pcb, openuav.kicad_sch]
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2023-08-12 Work in progress on new power supplies
    [openuav.kicad_pcb, openuav.kicad_sch]
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2023-08-12 More work on 36V power supplies
    [openuav.kicad_pcb, openuav.kicad_sch]
2023-08-12 Revert "More work on 36V power supplies"
    This reverts commit 1e05a41fa4dfa3787f584feb9a6f17393303f268.
    [openuav.kicad_pcb, openuav.kicad_sch]
2023-08-12 Revert "Work in progress on new power supplies"
    This reverts commit f380e0b659656c6729afb5916a220a1607aef7b0.
    [openuav.kicad_pcb, openuav.kicad_sch]
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2023-08-14 Add dual 9v / 5v power supplies
    [openuav.kicad_pcb, openuav.kicad_sch]
2023-08-15 Add remaining part numbers, temporarily downgrade baro due to availability
    [openuav.kicad_pcb, openuav.kicad_sch]
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2023-08-17 revert experimental gyro settings, add D term filter
    [gyro.c, main.c]
2023-08-18 Change 9V enable resistor to pull-down
    [openuav.kicad_pcb, openuav.kicad_sch]
2023-08-18 Update part number for baro
    [openuav.kicad_pcb, openuav.kicad_sch]
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2023-08-20 Move hardware design into a directory
    [HRO_TYPE-C-31-M-12.step, openuav.kicad_pcb, openuav.kicad_sch]
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2023-08-25 Move schematic PDF to correct location
2023-08-26 Update LEDs for v2 board, rework USB interface
    [flash.c, gpio.c, led.c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]
2023-08-26 Add three new OSD features:
    - one-letter indicator for armed/disarmed state
    - one-letter indicator for acro/angle mode
    - display "BATTERY!" in the middle of the screen once the voltage
    drops too much
    [main.c, msp.c]
2023-08-26 Remove SMPS in preparation for next attempt
    [openuav.kicad_pcb, openuav.kicad_sch]
2023-08-26 Begin TI SMPS design
    [RNX0012C.stp, openuav.kicad_pcb, openuav.kicad_sch]
2023-08-26 Work in progress new SMPS
    [openuav.kicad_pcb, openuav.kicad_sch]
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2023-08-26 Revert v1 hardware, remove unused code for v2 hardware
    [RNX0012C.stp, openuav.kicad_pcb, openuav.kicad_sch]
2023-08-27 Increase board size
    [openuav.kicad_pcb]
2023-08-27 Remove reset button
    [openuav.kicad_pcb, openuav.kicad_sch]
2023-08-27 Move pads to edge of board
    [openuav.kicad_pcb]
2023-08-27 Move DFU button
    [openuav.kicad_pcb, openuav.kicad_sch]
2023-08-27 Swap USB power diode for smaller part
    [openuav.kicad_pcb, openuav.kicad_sch]
2023-08-27 Finish v3 board design
    [openuav.kicad_pcb, openuav.kicad_sch]
2023-08-27 Continued work on configurator. Add missing blackbox_init call.
    [flash.c, main.c, usb.c]
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2023-08-27 Rework supply rail capacitors
    [openuav.kicad_pcb, openuav.kicad_sch]
2023-08-27 Replace LSM6DSO with LSM6DSR
    [openuav.kicad_pcb, openuav.kicad_sch]
2023-08-27 Move README, negligable PCB layout improvement
    [openuav.kicad_pcb]
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2023-09-02 Remove cell count guess and replace with configuration option
    [adc.c, main.c, msp.c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]
2023-09-02 Fixes for new gyro filtering changes
    [gyro.c, main.c]
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2023-09-09 Fix overflow in PID CSV export
    [main.c]
2023-09-09 Change IMU to ICM-42688-P. Change top and bottom planes to GND.
    [openuav.kicad_pcb, openuav.kicad_sch]
2023-09-11 PCB improvements
    [openuav.kicad_pcb]
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2023-09-16 Begin ESC hardware
    [esc.kicad_pcb, esc.kicad_sch]
2023-09-17 Continued work on ESC
    [esc.kicad_sch, single_esc.kicad_sch]
2023-09-18 Fix time output in configurator
    [main.c]
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2023-09-21 Fix time scaling in blackbox output
    [main.c]
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2023-09-23 Update example tune for new gyro, change air mode to avoid motors stopping in extreme cases
    [airmode.c]
2023-09-23 Remove ESC for now
    [esc.kicad_pcb, esc.kicad_sch, single_esc.kicad_sch]
2023-10-11 Add M10 GPS support This doesn't affect flight in any way yet but if a M10 GPS is connected, the power LED will flash and then turn solid when a 7-satellite lock is achieved. It exposes LAT and LONG 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
    [gpio.c, gpio.h, led.c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]
2023-10-11 Add barometer support This doesn't do anything yet but the data is now available for OSD and/or flight use.
    [barometer.c, main.c]
2023-10-11 Begin reworking angle mode for better feel and configurability
    [main.c]
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2023-10-14 Fixes to current display code
2023-10-18 Add missing newline at end of "get" output.
    [main.c]
